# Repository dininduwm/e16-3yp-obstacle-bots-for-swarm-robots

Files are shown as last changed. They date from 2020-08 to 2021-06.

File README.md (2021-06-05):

# Swarm Robotics Platform





### Team
* Members
   * Thushara K A R         :: E/16/369 :: [e16369@eng.pdn.ac.lk](e16369@eng.pdn.ac.lk)
   * Thilakarathna D M D U  :: E/16/366 :: [e16366@eng.pdn.ac.lk](e16366@eng.pdn.ac.lk)
   * Dissanayake D M T H    :: E/16/088 :: [e16088@eng.pdn.ac.lk](e16088@eng.pdn.ac.lk)
* Supervisor
   * Dr. Isuru Navinna
   * Mr. Ziyan Marikkar
   * Prof. Roshan Ragel
   * Dr. Upul Jayasinghe
* Related links
   * [Project Page](https://cepdnaclk.github.io/e16-3yp-obstacle-bots-for-swarm-robots/)
   * [Web Application Home Page](http://3.93.215.173/)
   * [Swarm Dash Board](http://3.93.215.173/swarm/)
   * [Faculty website](http://eng.pdn.ac.lk/)
   * [Department website](http://www.ce.pdn.ac.lk/)
   * [Design Manual](https://github.com/cepdnaclk/e16-3yp-obstacle-bots-for-swarm-robots/blob/master/Documentation/DesignManual.pdf)
   * [User Manual](https://github.com/cepdnaclk/e16-3yp-obstacle-bots-for-swarm-robots/blob/master/Documentation/UserManual.pdf)

### OVERVIEW

In swarm robotics the major barrier is that the researchers have to do a lot of hardware implementation prior to their projects. In this particular project we are going to come up with obstacle bots for a swarm robotic arena which is a part of a swarm robots platform project which eventually solves the above mentioned problem. 

### GOALS

* Automated obstacle bots monitored by an overhead camera setup.

* Bots can move to the desired positions with a user friendly interface.

### SPECIFICATIONS

* Obstacle robot swarm is capable of moving every individual obstacle robot to their own destination with the consideration of  collision  avoidance. 

* With the help of collision avoidance algorithms, obstacle robots can be placed in certain positions which allows the researcher to make  various obstacle shapes on the arena made out of obstacle robot combinations .

* Obstacles can be programmed to be static or dynamic. Dynamic obstacles can model scenarios that have a motion in the obstacle.

* Each robot has its own radio module  which uses a 433Mhz radio band. These modules can be used to communicate with the base station. 

* Each robot has two independent wheels that can perform forward, backward and turning operations. With the help of inbuilt gyroscope robots can perform accurate turning operations.

### SOLUTION ARCHITECTURE
    
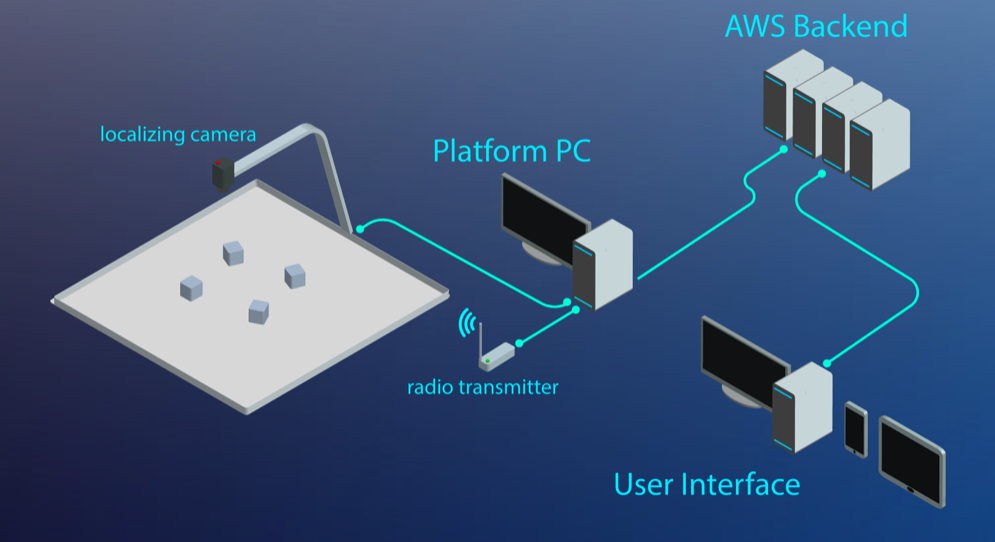
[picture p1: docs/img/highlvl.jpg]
robot_base_design
   
   
### HARDWARE
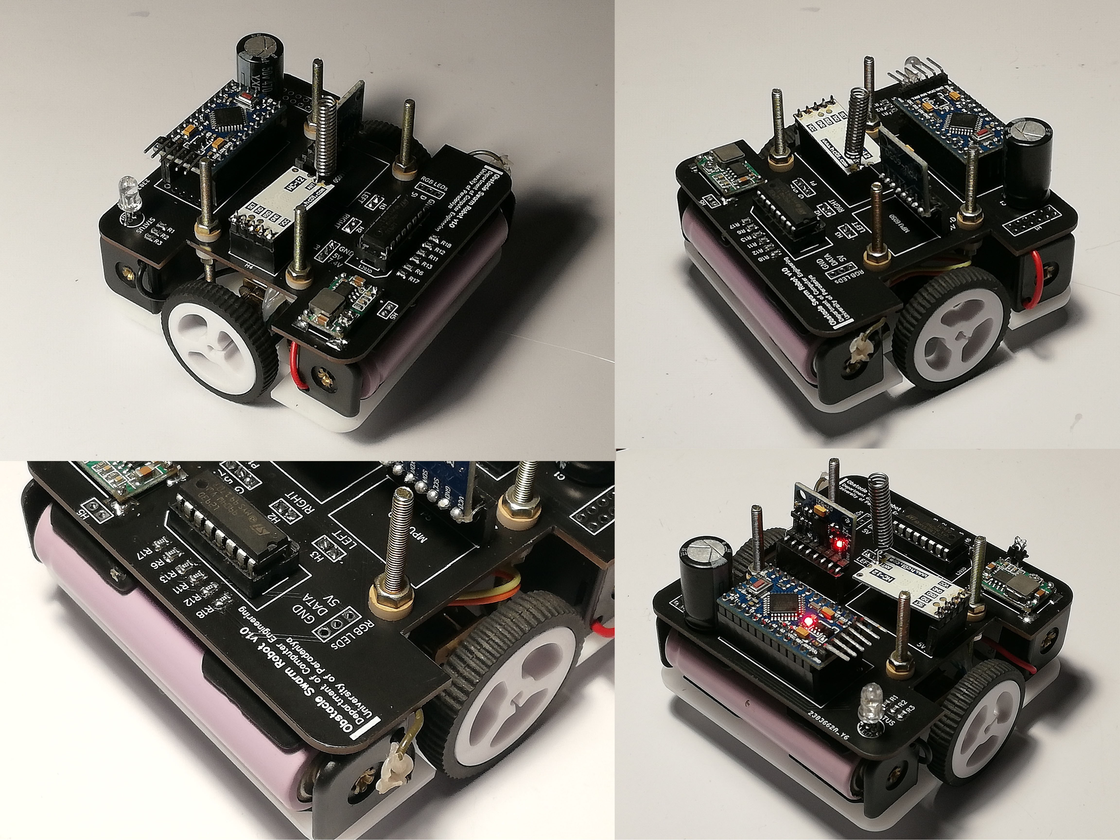
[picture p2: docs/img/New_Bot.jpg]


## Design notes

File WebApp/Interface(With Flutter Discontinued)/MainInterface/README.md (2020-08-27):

# MainInterface

A new Flutter project.

## Getting Started

This project is a starting point for a Flutter application.

A few resources to get you started if this is your first Flutter project:

- [Lab: Write your first Flutter app](https://flutter.dev/docs/get-started/codelab)
- [Cookbook: Useful Flutter samples](https://flutter.dev/docs/cookbook)

For help getting started with Flutter, view our
[online documentation](https://flutter.dev/docs), which offers tutorials,
samples, guidance on mobile development, and a full API reference.

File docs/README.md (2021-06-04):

# Swarm Robotics Platform

### Team
* Members
   * Thushara K A R         :: E/16/369 :: [e16369@eng.pdn.ac.lk](e16369@eng.pdn.ac.lk)
   * Thilakarathna D M D U  :: E/16/366 :: [e16366@eng.pdn.ac.lk](e16366@eng.pdn.ac.lk)
   * Dissanayake D M T H    :: E/16/088 :: [e16088@eng.pdn.ac.lk](e16088@eng.pdn.ac.lk)
* Supervisor
   * Dr. Isuru Navinna
   * Mr. Ziyan Marikkar
   * Prof. Roshan Ragel
   * Dr. Upul Jayasinghe
* Related links
   * [Faculty website](http://eng.pdn.ac.lk/)
   * [Department website](http://www.ce.pdn.ac.lk/)
   * [Web Application Home Page](http://3.93.215.173/)
   * [Swarm Dash Board](http://3.93.215.173/swarm/)
   * [Git Hub Repository](https://github.com/cepdnaclk/e16-3yp-obstacle-bots-for-swarm-robots)
   * [Design Manual](https://github.com/cepdnaclk/e16-3yp-obstacle-bots-for-swarm-robots/blob/master/Documentation/DesignManual.pdf)
   * [User Manual](https://github.com/cepdnaclk/e16-3yp-obstacle-bots-for-swarm-robots/blob/master/Documentation/UserManual.pdf)

### TABLE OF CONTENT

1. >[OVERVIEW](https://github.com/cepdnaclk/e16-3yp-obstacle-bots-for-swarm-robots#overview)
2. >[GOALS](https://github.com/cepdnaclk/e16-3yp-obstacle-bots-for-swarm-robots#goals)
3. >[SPECIFICATIONS](https://github.com/cepdnaclk/e16-3yp-obstacle-bots-for-swarm-robots#specifications)
4. >[SOLUTION ARCHITECTURE](https://github.com/cepdnaclk/e16-3yp-obstacle-bots-for-swarm-robots#solution-architecture)
5. >[HARDWARE](https://github.com/cepdnaclk/e16-3yp-obstacle-bots-for-swarm-robots#hardware)
6. >[WEB INTERFACE](https://github.com/cepdnaclk/e16-3yp-obstacle-bots-for-swarm-robots#software)
7. >[ALGORITHM](https://github.com/cepdnaclk/e16-3yp-obstacle-bots-for-swarm-robots#algorithm)
8. >[TESTING](https://github.com/cepdnaclk/e16-3yp-obstacle-bots-for-swarm-robots#testing)
9. >[BUDGET](https://github.com/cepdnaclk/e16-3yp-obstacle-bots-for-swarm-robots#budget)

### OVERVIEW

In swarm robotics the major barrier is that the researchers have to do a lot of hardware implementation prior to their projects. In this particular project we are going to come up with obstacle bots for a swarm robotic arena which is a part of a swarm robots platform project which eventually solves the above mentioned problem. 

### GOALS

* Automated obstacle bots monitored by an overhead camera setup.

* Bots can move to the desired positions with a user friendly interface.

### SPECIFICATIONS

* Obstacle robot swarm is capable of moving every individual obstacle robot to their own destination with the consideration of  collision  avoidance. 

* With the help of collision avoidance algorithms, obstacle robots can be placed in certain positions which allows the researcher to make  various obstacle shapes on the arena made out of obstacle robot combinations .

* Obstacles can be programmed to be static or dynamic. Dynamic obstacles can model scenarios that have a motion in the obstacle.

* Each robot has its own radio module  which uses a 433Mhz radio band. These modules can be used to communicate with the base station. 

* Each robot has two independent wheels that can perform forward, backward and turning operations. With the help of inbuilt gyroscope robots can perform accurate turning operations.

### SOLUTION ARCHITECTURE
    
   robot_base_design

### HARDWARE

 * #### REAL HARDWARE
    robot_base_design

   STATUS _LED
 * #### 3D MODEL
 
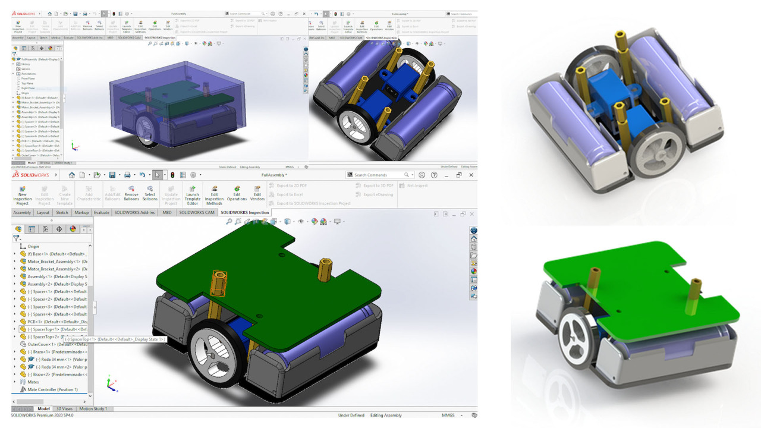
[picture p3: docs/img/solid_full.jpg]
MODEL
   
   
   [3D MODEL DEMO VIDEO](https://drive.google.com/file/d/1BgqnTfJoUTvxhPZTlfKIsdu9cmKUDJUL/view?usp=sharing)

 * #### SAFTY MEASURES

    IMERGENCY STATUS

* #### PCB DESIGN

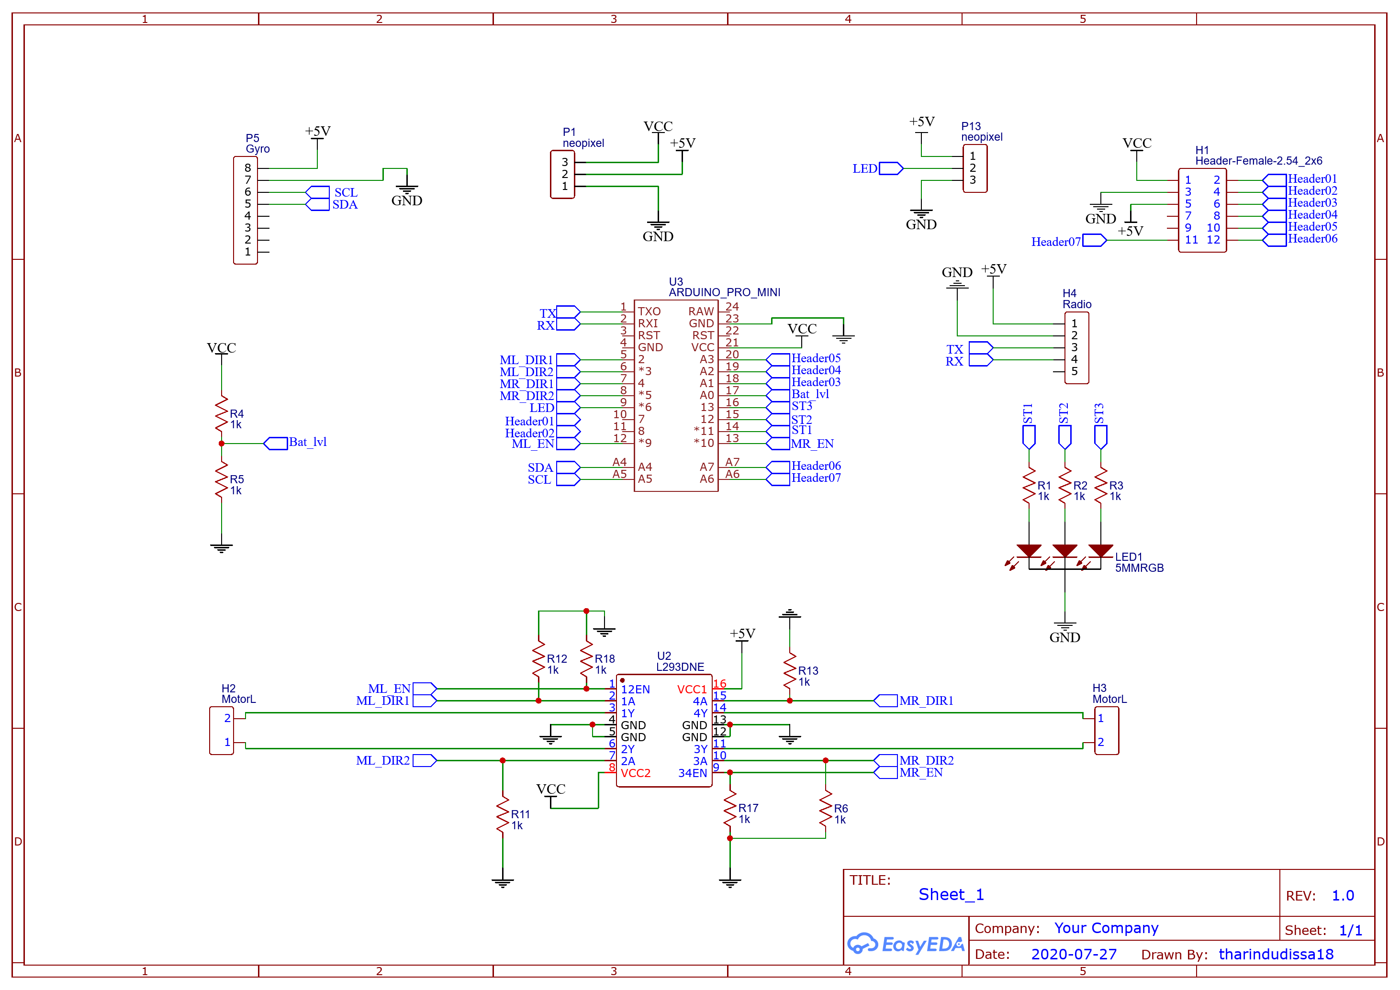
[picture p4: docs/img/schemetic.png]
PCB
  

  PCB
  
  [PCB DEMO VIDEO](https://drive.google.com/file/d/1F948O53cgekAJtsLhbUBktsmgBemvtih/view?usp=sharing)
  
### WEB INTERFACE

   #### Web Interface

   [WEB INTERFACE DEMO VIDEO](https://drive.google.com/file/d/1p-WY_BGf4mX0sW0hUGA0x1Oh4LhzKp-s/view?usp=sharing)

   #### 3D Interface

   [3D INTERFACE DEMO VIDEO](https://drive.google.com/file/d/1X0jq2r_McNR5bppIPc1HjJY1mYPvrYJg/view?usp=sharing)
  
   #### Platform PC Operator GUI

   [3D INTERFACE DEMO VIDEO](https://drive.google.com/file/d/1NqZ_JTVdCaxA32IgvhgPbMnpfuTEIJsR/view?usp=sharing)
  
### ALGORITHM

  ALGORITHM
  
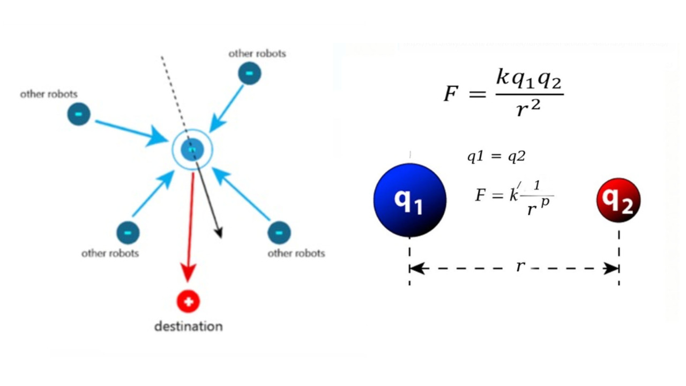
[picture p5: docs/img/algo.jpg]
THEORY
  
  
### TESTING
  
   #### Algorithm Deployment

   [Algorithm Deployment Video](https://drive.google.com/file/d/18J7mnoRWbKy1-WM-fGOGq0C8-KU52HCJ/view?usp=sharing)
  
   #### Web Interface Authentication And Authorization Testing

   [Web Interface Testing Video](https://drive.google.com/file/d/12DfR7rRFpMq2U1c6BGW0rHfQw0c6rsvO/view?usp=sharing)
  
   #### Hardware Testing

   [Hardware Testing Video](https://drive.google.com/file/d/1UNAkzgOKk-umYvnypkwuJJWv3zXbf69Z/view?usp=sharing)
  
### BUDGET
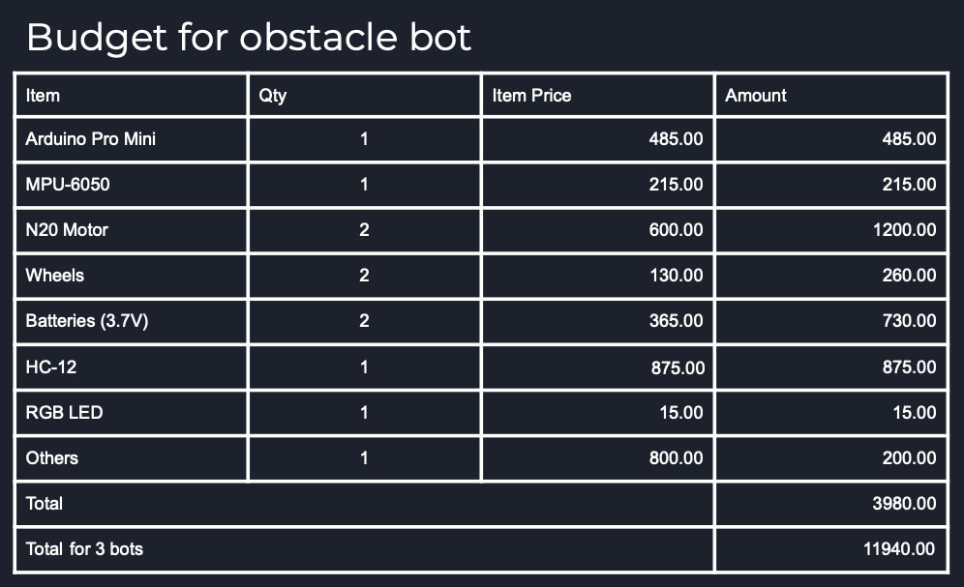
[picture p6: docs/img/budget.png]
BUDGET
  

### FINAL DEMO VIDEO
  [Final Demo Video](https://drive.google.com/file/d/1B5mBls3YdkssftkCu0zrgztlk1W86l-X/view?usp=sharing)
  
### FUTURE IMPROVEMENT
  We plan to run all the algorithms first and then send the data to the robots.
  
  We have to further tune the parameters  to get a smooth process.

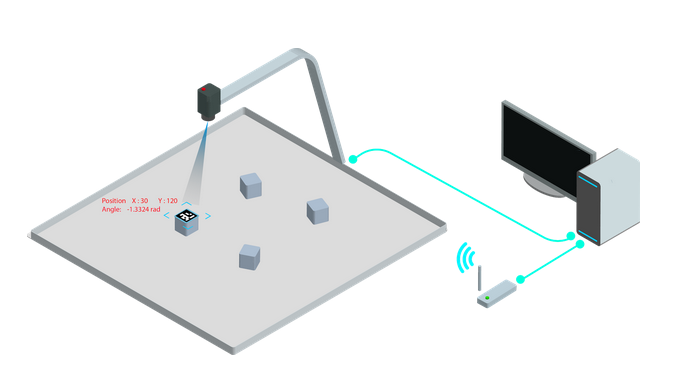
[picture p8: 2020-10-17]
3DModel/Components/Design_Diagrams/robot_arena.png

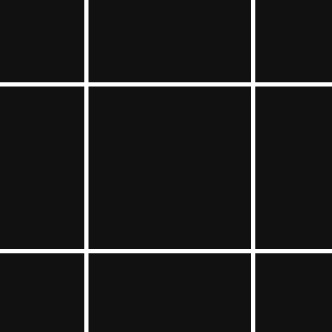
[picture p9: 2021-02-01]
3D_Interface/resources/images/light.jpg

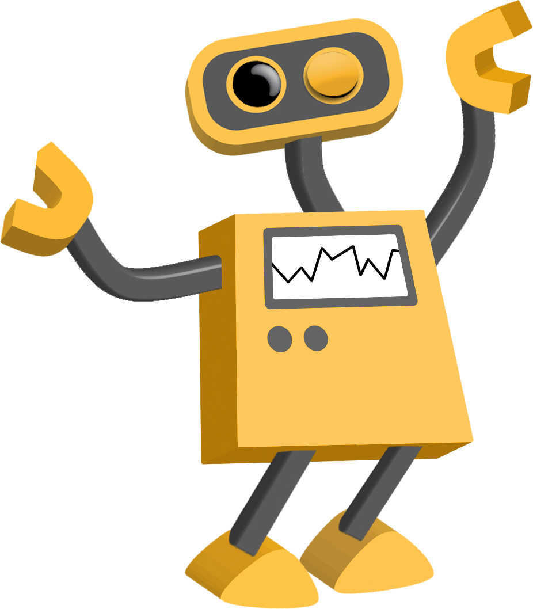
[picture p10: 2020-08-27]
WebApp/Interface(With Flutter Discontinued)/MainInterface/assets/welcomebot.png

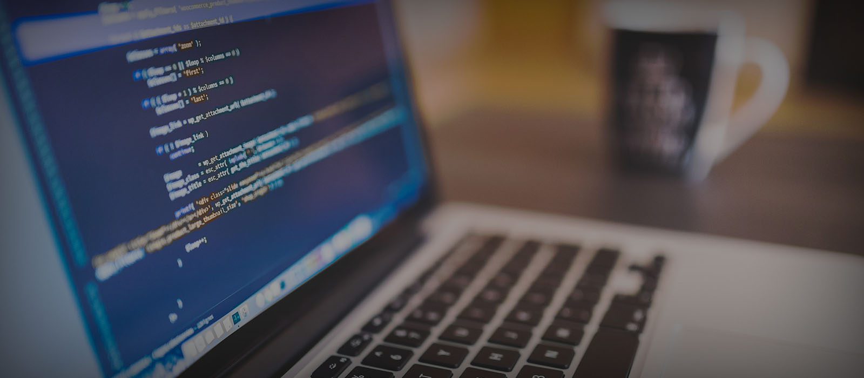
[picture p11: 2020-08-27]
WebApp/Interface(With Flutter Discontinued)/MainInterface/assets/background.jpg

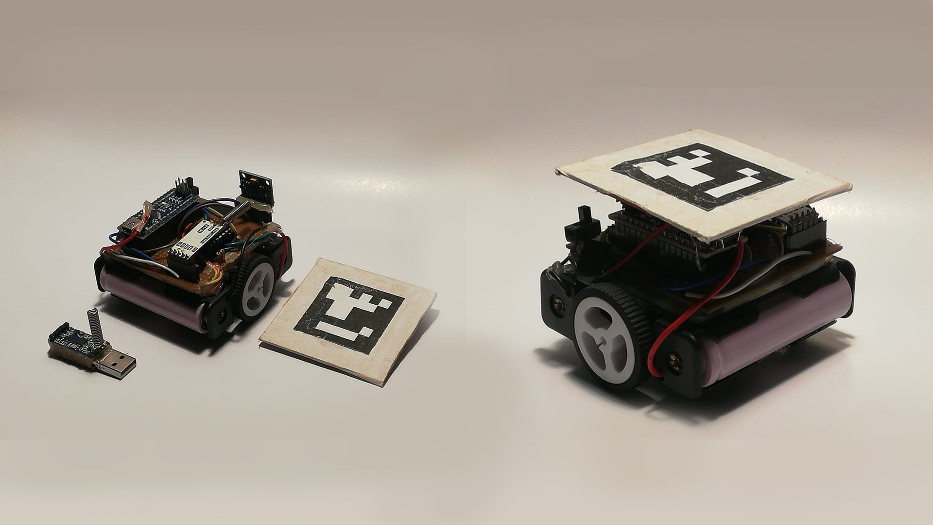
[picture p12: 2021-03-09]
docs/img/proto.jpg

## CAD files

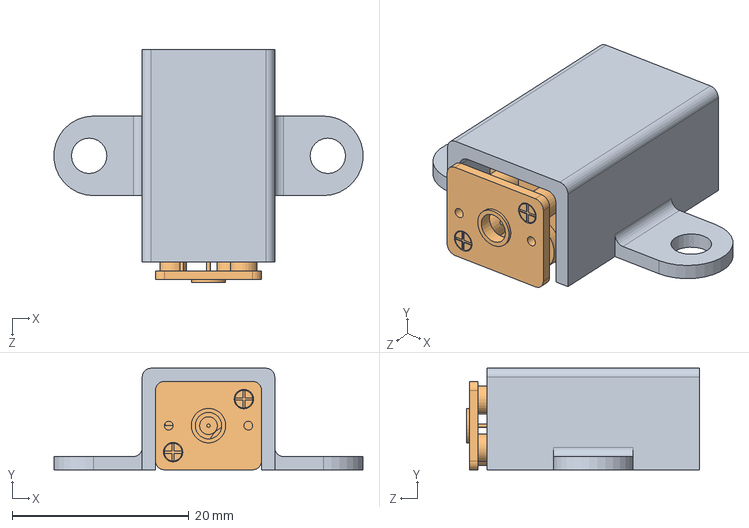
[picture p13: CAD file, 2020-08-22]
3DModel/Components/Motor_Bracket_Assembly/Motor_Bracket_Assembly.SLDASM
35.0 x 11.5 x 26.3 mm
braket pololu
Motor

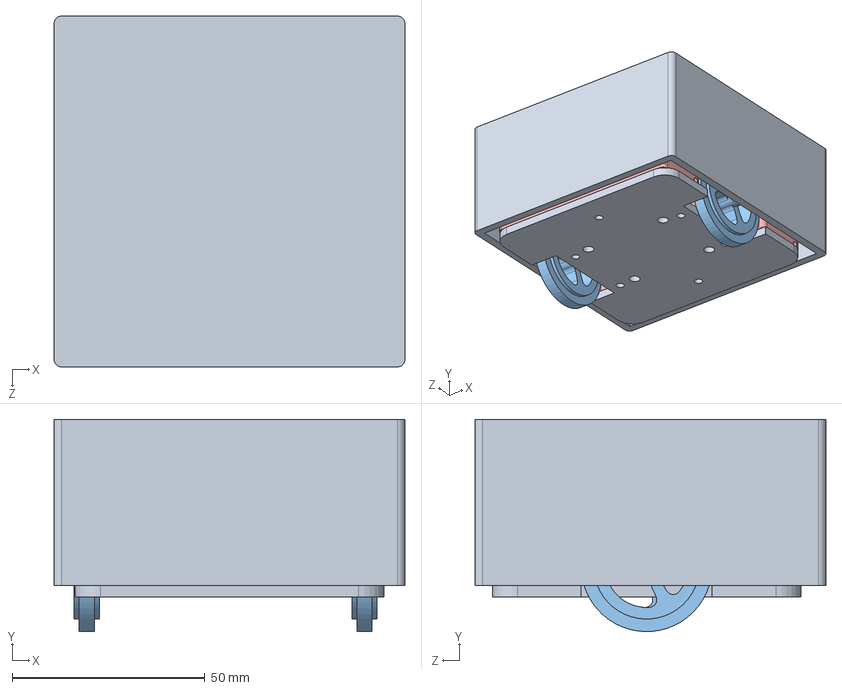
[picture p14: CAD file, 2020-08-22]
3DModel/FullAssembly.SLDASM
91.0 x 55.0 x 91.0 mm
Base
braket pololu x 2
Motor x 2
18650BatteryCase v6.step x 2
Spacer x 4
PCB
SpacerTop x 2
OuterCover
Brazo x 2
Roda 34 mm x 2

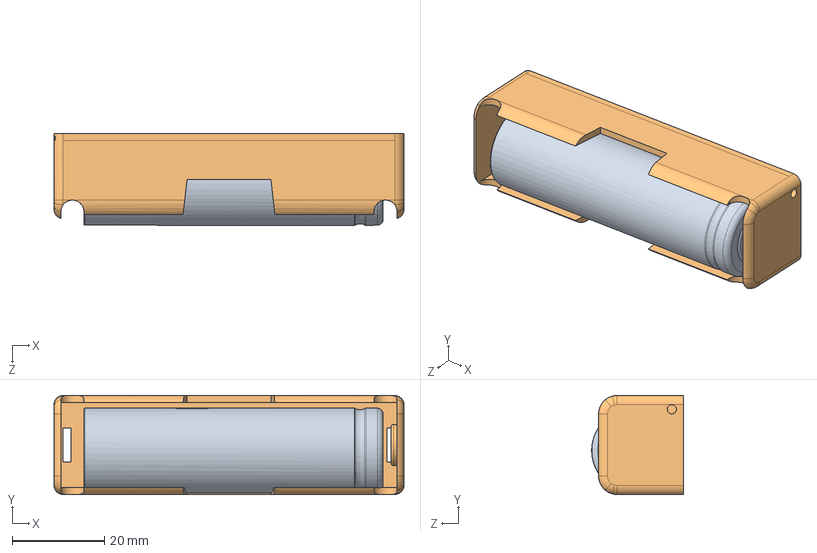
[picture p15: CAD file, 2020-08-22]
3DModel/Components/18650WithCasin/Assembly.SLDASM
76.0 x 21.5 x 19.9 mm
18650BatteryCase v6.step

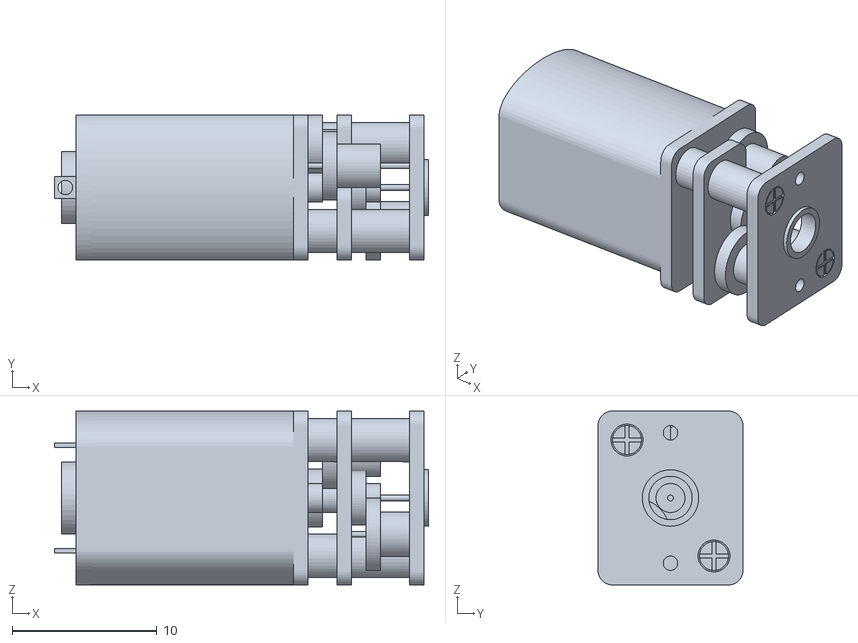
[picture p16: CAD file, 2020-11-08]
3D_Interface/resources/3DModels/motor.STL
25.8 x 10.00 x 12.0

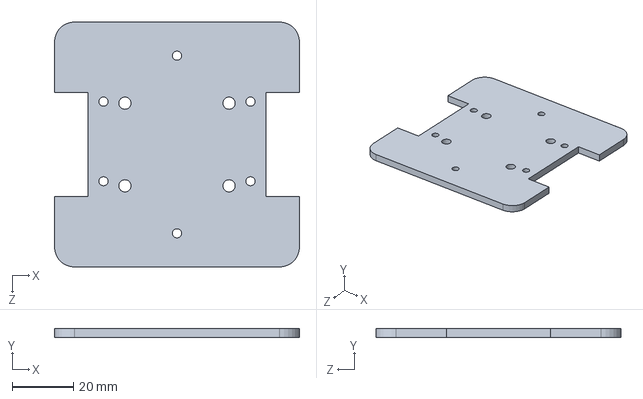
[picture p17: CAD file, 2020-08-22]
3DModel/Components/Base/Base.SLDPRT
80.0 x 3.00 x 80.0 mm

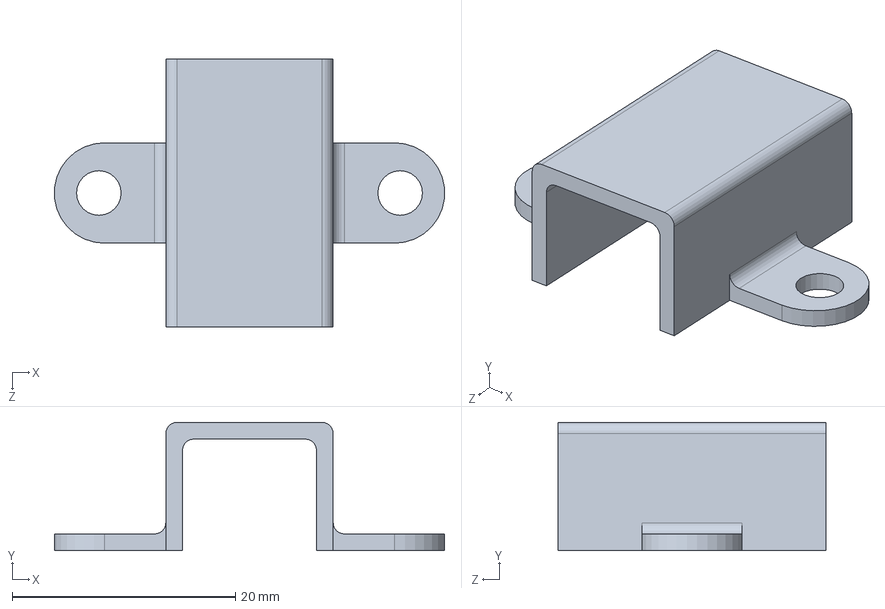
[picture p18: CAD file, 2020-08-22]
3DModel/Components/N20_Bracket/braket pololu.SLDPRT
35.0 x 11.5 x 24.0 mm

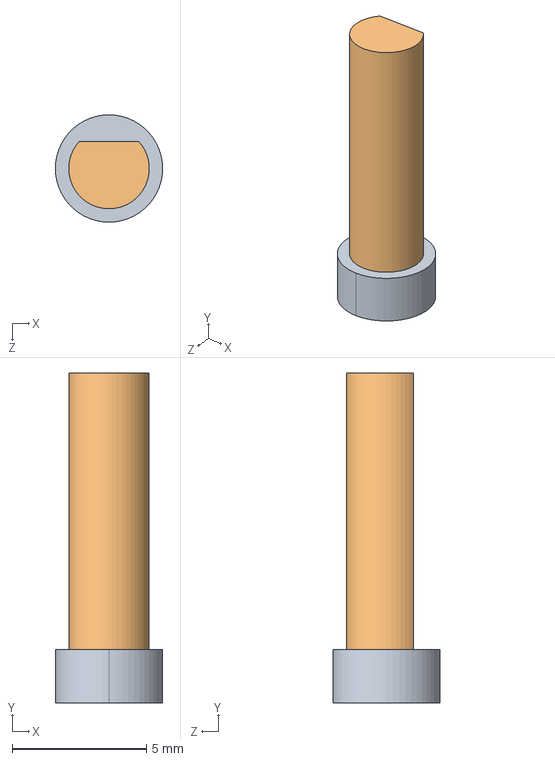
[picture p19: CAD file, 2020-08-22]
3DModel/Components/N20_Motor/Brazo M.STEP
4.00 x 12.3 x 4.00 mm

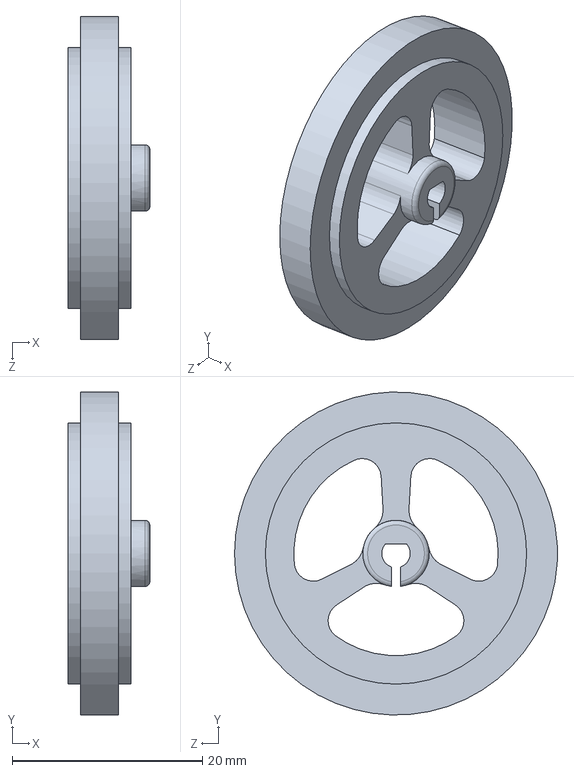
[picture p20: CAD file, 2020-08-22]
3DModel/Components/N20_Wheel/Roda 34 mm.SLDPRT
8.60 x 34.0 x 34.0 mm

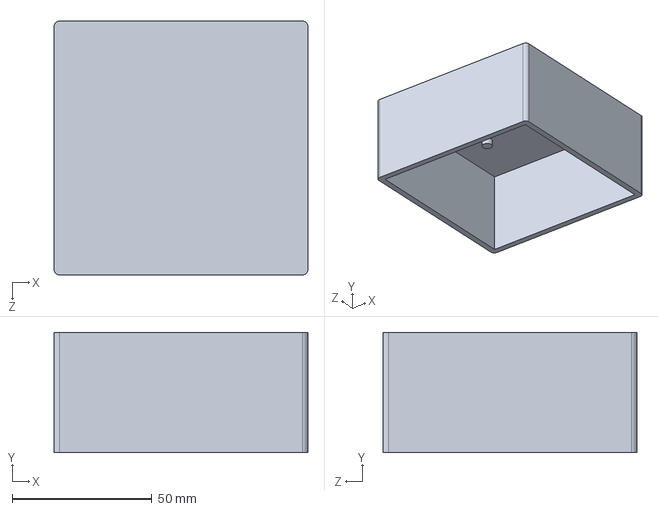
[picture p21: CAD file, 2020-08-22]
3DModel/Components/OuterCover/OuterCover.SLDPRT
91.0 x 43.0 x 91.0 mm

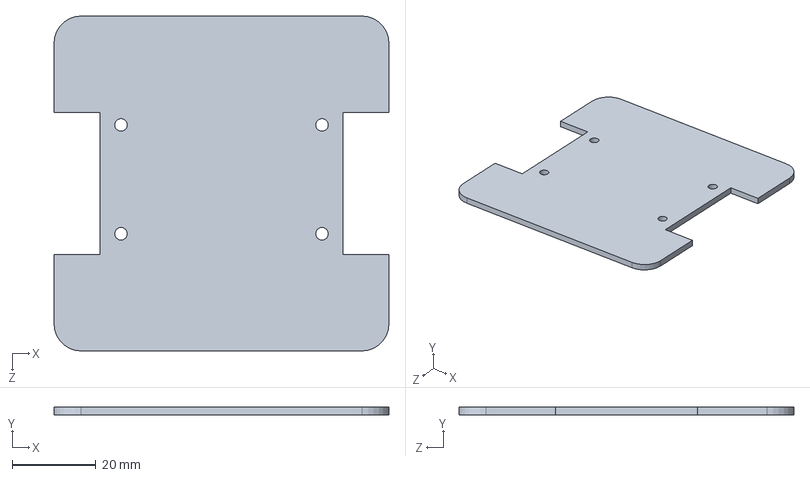
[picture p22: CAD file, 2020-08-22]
3DModel/Components/PCB/PCB.SLDPRT
80.0 x 2.00 x 80.0 mm

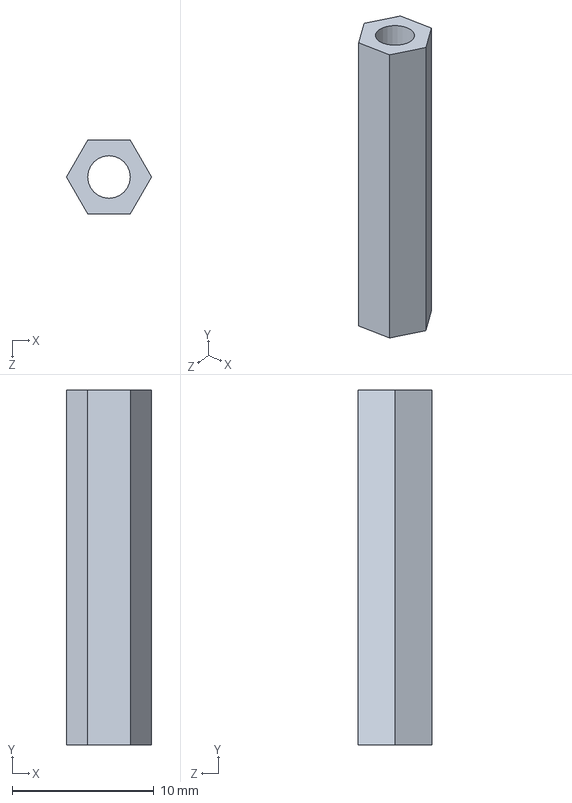
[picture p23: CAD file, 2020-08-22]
3DModel/Components/Spacer/Spacer.SLDPRT
6.00 x 25.0 x 5.20 mm

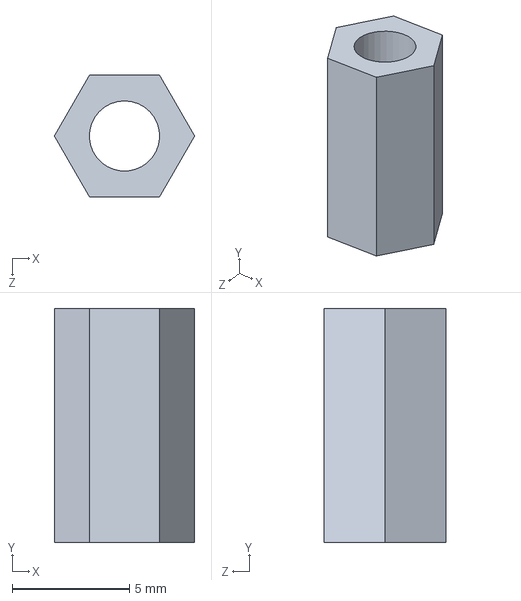
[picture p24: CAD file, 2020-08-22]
3DModel/Components/SpacerTop/SpacerTop.SLDPRT
6.00 x 10.0 x 5.20 mm

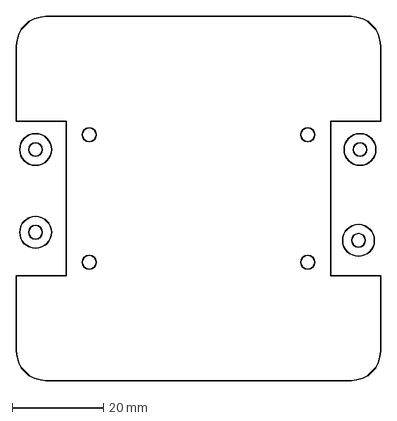
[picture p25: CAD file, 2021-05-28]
Fabrication/Laser Cutting/BasePlate/bot.dxf
80.0 x 80.0 mm

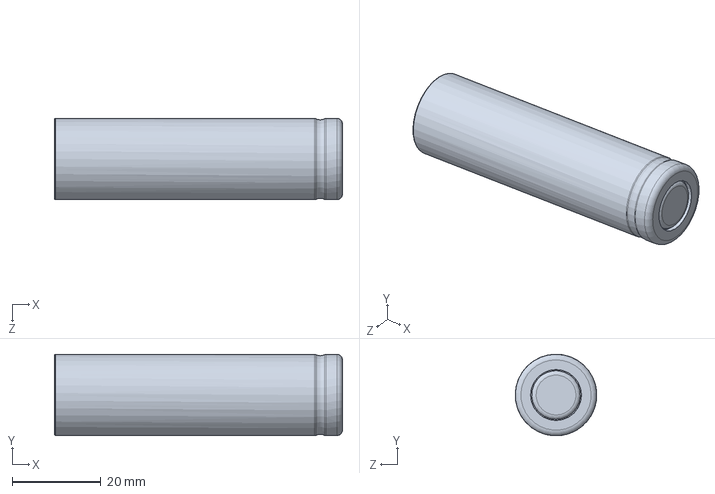
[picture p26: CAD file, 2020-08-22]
3DModel/Components/18650WithCasin/18650.SLDPRT
65.0 x 18.4 x 18.4 mm

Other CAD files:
WebApp/MainWebApp/static/swarm/Cover.91c86dd7.STL
3DModel/Components/N20_Motor/Brazo.SLDPRT
3DModel/Components/N20_Motor/Motor M.STEP
3DModel/Components/N20_Motor/Motor.SLDPRT
3DModel/Components/18650WithCasin/18650BatteryCase v6.step

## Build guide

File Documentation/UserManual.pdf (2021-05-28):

# User Manual

# Obstacle Robots For Swarm Robots Platform

May 2021

ISSUED BY
Department of Computer Engineering, University of Peradeniya.

REPRESENTATIVE
E/16/369 Rusiru Thushara
E/16/366 Dinindu Thilakarathne E/16/088 Heshan Disanayake

# Content

1. Introduction & Background | 3
2. Features | 4
3. Quick Startup | 5
4. Device Installation | 7
5. Operator GUI | 8
6. Web Interface | 9
6.2. | Indicators | |
| 10

### 6.3.3. Removing a destination | 12

6.3.4. | Remove all destinations | | 12

### 6.3.5. Changing the robot’s colour | 12

7. Robot | | 13

### 7.1. Overview | 13

8. Troubleshooting | 15

### 8.1. Camera position troubleshooting | 15 8.2. AR marker detection troubleshooting | 15 8.3. Local communication troubleshooting | 15 8.4. Robottroubleshooting | 16

# List of Figures

Figure 1: High-Level Diagram | 3
Figure 2: Operator GUI | 8
Figure 3: Web interface | 10
Figure 4: Overview ofthe robot | 13

# 1. Introduction and Background

### 1.1. Process Overview

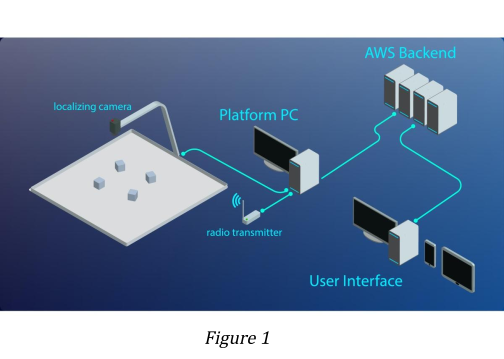
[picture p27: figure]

The system uses an overhead camera to localize the robots and the video feed is sent to the platform PC where all the algorithms are running and calculating the required parameters and the relevant data to the robots are sent using radio transmission and the other required data is sent to the server backend.

### 1.2. The System

The system contains a radio transmitter module, camera module, and robots. You should have to have an arena for the given dimensions. If your arena dimensions are higher than the given dimensions you have to purchase a separate HD overhead camera module. You have to have a computer ( not included with the product ) with an internet connection.

# 2. Features

- Algorithms are capable of handling about 100 robots.
- Self homing feature when the battery levels are too low.
- Battery level monitoring feature with GUI.
- Hardware and software emergency stop buttons.
- User-friendly 3D web interface.
- User-friendly operator GUI.
- Compact robot designing.
- Highly accurate positioning of robots.
- Colour changing capability of robots.
- Automatic error detections of robots.

# 3. Quick Startup

This section explains the quicker way to set up the system to use

### 1. Setting up the overhead camera

Overhead camera should be fixed about 2m from the top surface of the arena. Then the USB cable should connect to the platform PC. (Camera calibration have to be done after step 2)

### 2. Installing and setting up the operator GUI

a. First, you have to install and set up python3 and pip3 in your system.
b. Then you have to clone this repository. https://github.com/cepdnaclk/e16-3yp-obstacle-bots-for-swarm-robots.git
c. Then change the directory to,/Platform_PC_Software/MainCode/

cd /Platform_PC_Software/MainCode/
d. Next open a terminal in that directory and enter the following command

pip3 install -r req.txt

### 3. Installing and setting up the radio transmitter module

a. You have to plugin the provided radio transmitter module to a USB port on the Computer
b. You have to identify the COM port for the usb device

### 4. Starting the Operator GUI for the firsttime

a. You will be prompted to enter the Swarm Name, Swarm ID, and the COM Portfor the radio transmitter module.
b. Now you can see the Operator GUI for the First time.

### 5. Adjusting the camera position

a. You have to adjust the camera position in such a way that the whole camera feed fits to the camera view.

b. Next place a bot inside the arena (Don’t turn on the robot yet). Observe the camera feed and verify the AR marker has been identified. (If identified, you can see a green square around the marker )

### 6. Turning on the robot

a. Now you can turn on the robot.
b. Then click the start button on the Operator GUI.
c. Then the robot should turn to a 90-degree angle and the status light should turn into cyan colour.
d. Now click on the home button in the control panel.
e. Then the robot should be moved into the home position.
(Note:- If you have any issues please refer to the troubleshooting section)

# 4. Device Installation

### 4.1. Power Requirements

- You have to install two 18650 Li-ion batteries on a robot. You have to charge each and every battery for at least 3 hours.
- A 24v power supply should be connected to the status lamp.

### 4.2. Network Configuration

- Platform PCs should always be connected to the internet. ( No other specific configuration needed )

### 4.3. Configuring Camera Setup

- The camera should be fixed, about 2m from the top surface of the arena.
- Then adjust the camera view by looking at the camera image in the Operator GUI (the whole arena should be visible through the camera view )
- Then you have to place a robot inside the camera view ( Without turning on the robot )
- Make sure the robot is identified by the Operator GUI by drawing a green square around the AR marker.
(Note:- If the markers are not detecting. Please refer to the camera troubleshooting section)

### 4.4. Radio Transmitter Installation

- The radio transmitter should be plugged into a USB port
- You should find the COM port for the transmitter
- You will be prompted to ask the COM port of the radio transmitter when opening the Operator GUI.

### 4.5. Emergency Stop and Status Lamp Installation

- The status lamp should be fixed on the arena
- Emergency stop should be fixed near to the operator
- Both of them should be connected to the radio transmitter module.
- Given 24V power supply should be connected to the status lamp.

# 5. Operator GUI

### 5.1. Overview

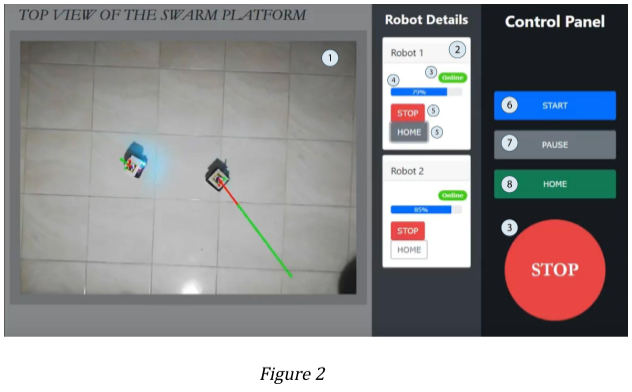
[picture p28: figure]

1 - Live view
2 - Robot details
3 - Robotlive status
4 - Battery percentage

5 - Individual Stop
6 - Individual Home
7 - Start button
8 - Pause button

9 - All Home Button
10 - All Stop Button

### 5.2. Indicators

The operator can check the battery status of the robots using the [4] battery status progress bar. Also, use the [3] status indicator to check the online/offline status of the robots.

### 5.3. Controlling

- Adding a new robot

The system will auto-detect a robot once you are adding a new robot to the system.
- Homing a robot
Press button 5 of individual robots to move the individual robot to the home position.
- Software emergency stop
Press the emergency stop button (button no. 3) to stop all the robots in an emergency.
- Starting and pausing a sequence
Press button 6 and 7 to start and pause the robots.

# 6. Web Interface

### 6.1. Overview

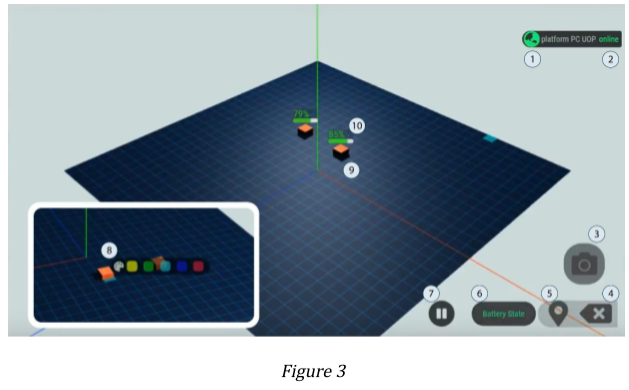
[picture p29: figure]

1 - Server name
2 - Server status
3 - Camera controller
4 - Destination clear

5 - Destination setter
6 - Battery status
7 - Pause button
8 - Robot colour picker

9 - Robot
10 - Battery level

### 6.2. Indicators

- Server Status

The status of the server can be seen in this tag. The globe will be animated if the server is online. Also, you can see the platform name in this tag.

- Robot Battery status

The battery status of the robot can be activated through the battery status button.

### 6.3. Controlling 6.3.1. Change the camera view

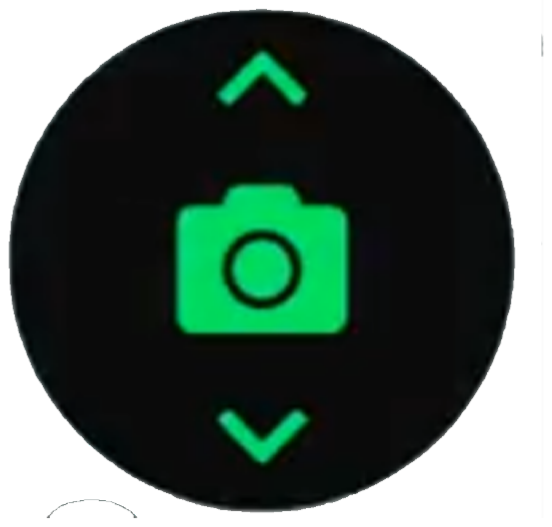
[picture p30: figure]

This is the controller for the camera view. The upper arrow has the control to align the camera view to the top view. And the middle camera logo is the button for isometric camera angle(camera home).

### 6.3.2. Setting a destination

To set the destinations you have to first toggle into destination set mode by clicking this button. Then you can set the destinations up to the count of robots by clicking on the arena. After deciding the destination positions you can release this button to transmit the destination data to the platform PC.

### 6.3.3. Removing a destination

To remove a single destination, click the destination button to go to the destination set mode. Then click on the destination you need to remove. Then the indication of the destination will go away.

6.3.4. Remove all destinations.

Click on this button to remove all destinations.

### 6.3.5. Change the color

To change the color, hover over the color pallet to get the color selecting option.choose a color you want .

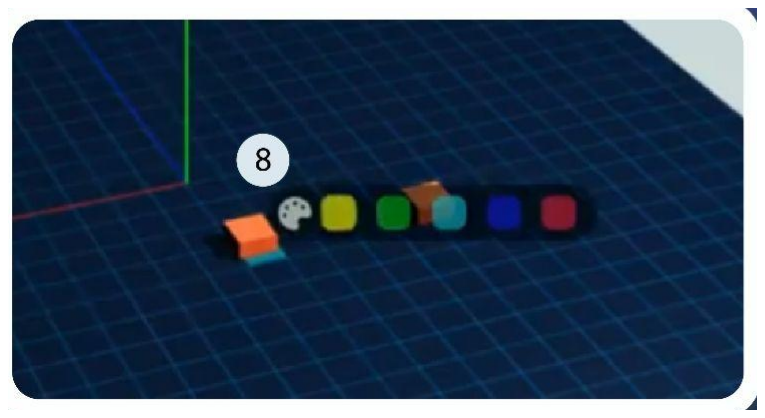
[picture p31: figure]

# 7. Robot

7.1. Overview

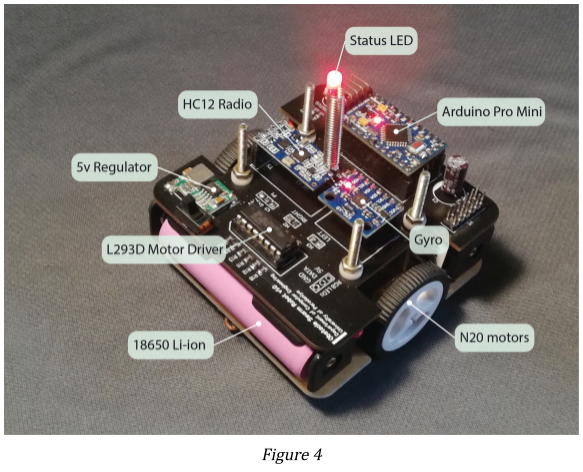
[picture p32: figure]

- Arduino pro mini
- Arduino 328p 16mhz microcontroller is used as the computer of this robot
- HC12 Radio module
- The radio communication is done with a 433Mhz HC-12 module. This is the transceiver that has the capability of 2-way communication with the platform PC.
- Gyroscope
- MPU 6050 is the gyroscope module used in this robot.

- 5v Regulator.
- Switch Mode 5v voltage regulator.
- Motor driver
- L293D is the motor driver IC used in this robot. Since this is the D version internal circuitry is safe from the flyback voltages.
- Batteries
- This robot is powered with 2s 18650 2000mah Li-ion battery.
- Motors
- This robot has two N20 100rpm 6v motors with 30mmx7mm wheels.
- Status LED
- Red blinking - robot successfully received a data packet.
- Blue blinking - robot successfully received a data packet that belong to the specific robot.
- Green - robot is in the turning PID loop.
- Light Blue - Robot at the destination.
- Extension port
- For the further development the unused pins of the arduino are extended via male 6x2 header the pin description is as follows.

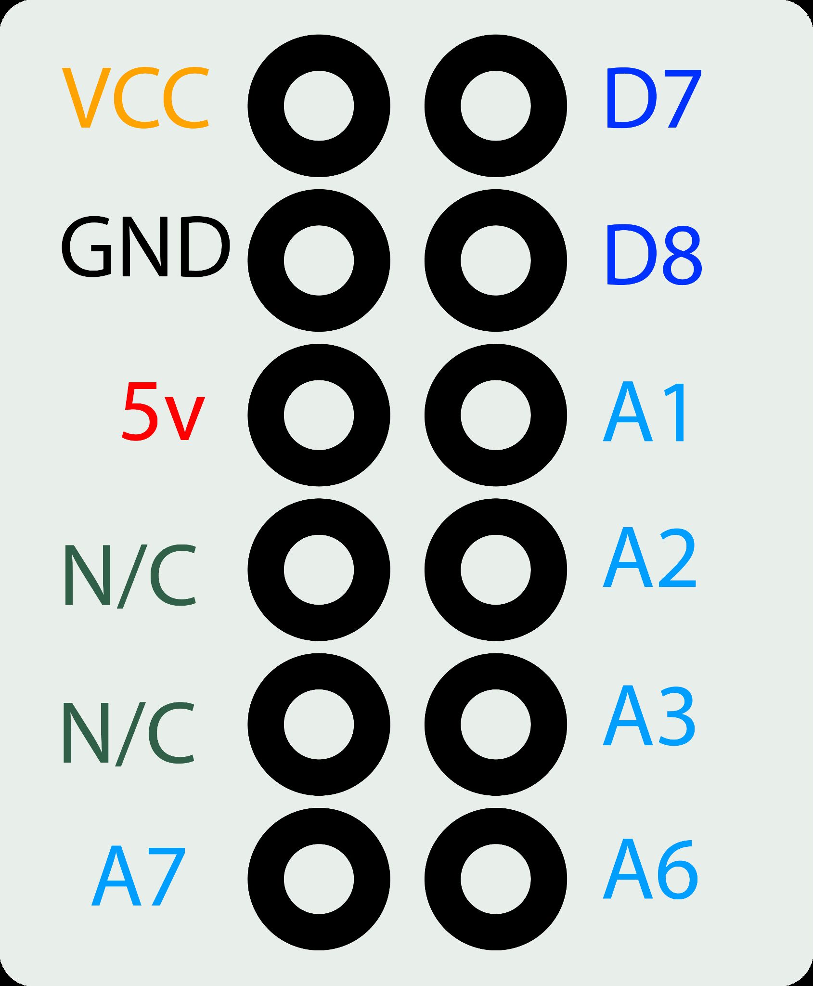
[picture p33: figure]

# 8. Troubleshooting

### 8.1. Camera position troubleshooting

Problem | Solution
Camera view detecting only part of the arena | ● Move the camera upwards until you can see the whole arena ● Center the camera module in the Arena
Camera not detecting | ● Unplug the USB cable and plug it again
Camera feed interruption ( or lagging ) | ● Check for the CPU usage of the system. If the CPU usage is above 80%, kill unwanted processes.

### 8.2. AR marker detection troubleshooting

Problem | Solution
AR Markers not detecting | ● Adjust the lighting conditions ● Move the camera closer to the Arena

### 8.3. Local communication troubleshooting

Problem | Solution
If the blue LED on the transmitter not blinking rapidly | ● Unplug the radio transmitter and plug it again ● Check whether the COM port is correct
Robotsred light not blinking | ● Check whether the Robot ids are correct in the Operator GUI ● Reset the Robot

- Reduce the distance between the radio transmitter and the Arena
- Check the radio transmitter module is firmly attached to the PCB

### 8.4. Robottroubleshooting

Problem | Solution
Not turning ON | ● Check whether the batteries are charged ● Check the batteries are installed in the correct way
One or both wheels not turning | ● Check the pugs connected to the motors are firmly attached to the PCB ● Check the wheels are firmly attached to the motor ● Check the battery level.
Robot is oscillating | ● Run the robot calibration programme

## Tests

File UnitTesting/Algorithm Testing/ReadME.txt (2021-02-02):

######
This will test the collition avoiding and positioning algorithm.

Cange the required bot count in the UnitTest.py file
Then, run the UnitTest.py

> python3 UnitTest.py

######

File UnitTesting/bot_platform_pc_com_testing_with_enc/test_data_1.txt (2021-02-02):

{'1': [118, 115, 85, 22], '2': [135, 320, 400, 291]}
{'1': [416, 49, 226, 333], '2': [207, 338, 443, 345]}
{'1': [260, 187, 94, 340], '2': [206, 324, 171, 8]}
{'1': [285, 288, 188, 8], '2': [313, 171, 381, 201]}
{'1': [301, 162, 341, 261], '2': [103, 193, 198, 201]}
{'1': [181, 167, 330, 13], '2': [66, 84, 172, 185]}
{'1': [30, 199, 179, 2], '2': [68, 274, 62, 169]}
{'1': [133, 124, 178, 68], '2': [272, 192, 247, 96]}
{'1': [323, 163, 446, 321], '2': [125, 68, 192, 157]}
{'1': [188, 290, 338, 40], '2': [61, 326, 78, 336]}

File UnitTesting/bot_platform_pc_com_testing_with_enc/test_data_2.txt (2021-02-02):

b'serial test 0021\r\n'
b'1,118,115,85,22,\n'
b'2,135,320,400,291,\n'
b'1,416,49,226,333,\n'
b'2,207,338,443,345,\n'
b'1,260,187,94,340,\n'
b'2,206,324,171,8,\n'
b'1,285,288,188,8,\n'
b'2,313,171,381,201,\n'
b'1,301,162,341,261,\n'
b'2,103,193,198,201,\n'
b'1,181,167,330,13,\n'
b'2,66,84,172,185,\n'
b'1,30,199,179,2,\n'
b'2,68,274,62,169,\n'
b'1,133,124,178,68,\n'
b'2,272,192,247,96,\n'
b'1,323,163,446,321,\n'
b'2,125,68,192,1571,188,290,338,42,61,326,78,336\r\n'

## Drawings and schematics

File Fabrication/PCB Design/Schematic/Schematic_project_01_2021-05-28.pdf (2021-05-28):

# VCCBATT

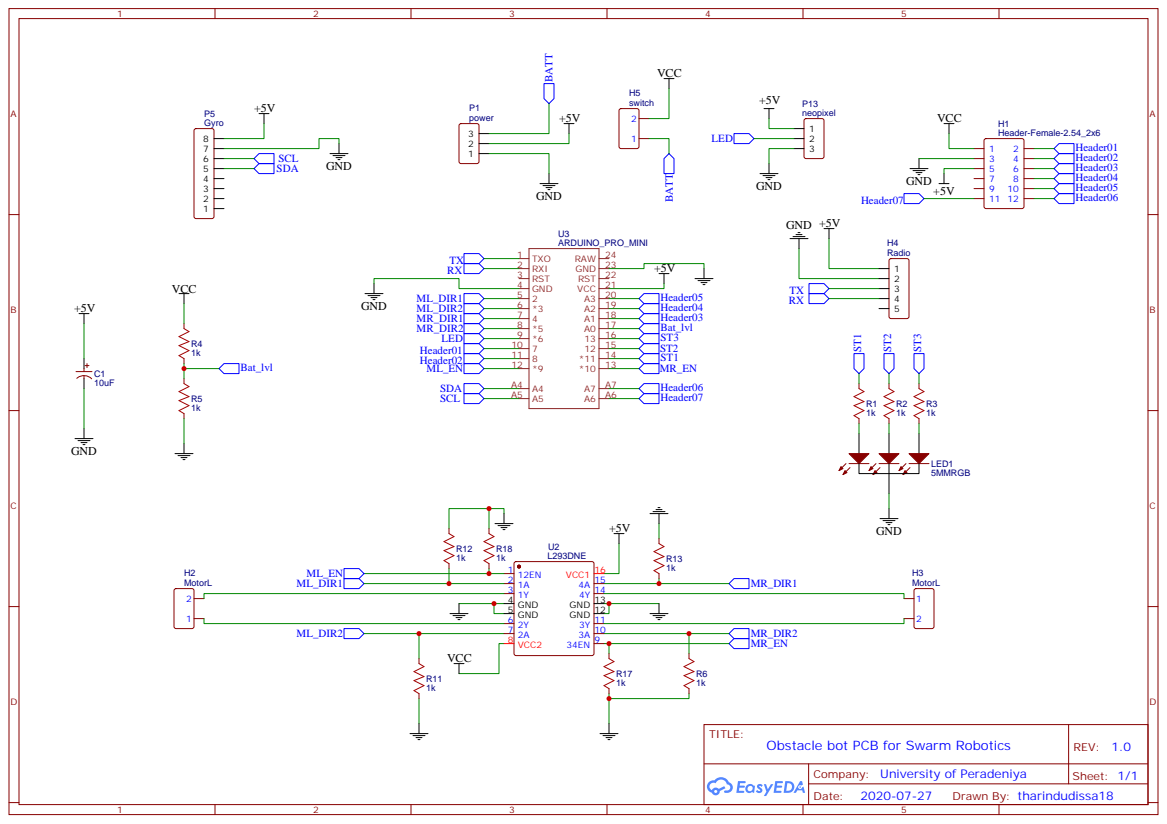
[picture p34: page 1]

Company: University of Peradeniya

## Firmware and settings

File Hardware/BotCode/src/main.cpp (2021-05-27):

#include <PID_v1.h>
#include <Wire.h>

#define EN_R 9  // right motor enable
#define EN_L 10 // left motor enable

#define ML_A1 5 // left motor in 1
#define ML_A2 4 // left motor in 2

#define MR_A1 3 // right motor in 1
#define MR_A2 2 // right motor in 2

#define led_r 11 // status leds
#define led_g 12
#define led_b 13

const float turningThresh = 0.15; // threshold to stop turning
const double distThresh = 20;     // threshold to stop moving
const int MPU = 0x68;             // MPU6050 I2C address
float GyroX, GyroY, GyroZ;
float angle;                                  // Gyro angle
float GyroErrorX;                             // Gyro error
float elapsedTime, currentTime, previousTime; // time stamps for gyro calculaions
int c = 0;

bool idflag = false;
String id = "";
double arr[3]{};   // arr to hold startAngle, travelDis, endAngle
int idx = 0;     // index to track the arr index
bool good = false; // bool to check the correct id

//json decoded
double startAngle, endAngle, travelDis;

//PID variables
double Setpoint, Input, Output;
bool newData = false;

// id of the bot
String myID = "1";

// creating software serial object


// variables to hold temp data
String reciveStr = "";

//PID configuration
PID myPID(&Input, &Output, &Setpoint, 16, 0, 0.23, DIRECT);

void ML(int val)
{ // motor function left(val : speed value)

  //handle overflow in val
  if (val < -255)
  {
    val = -255;
  }
  else if (val > 255)
  {
    val = 255;
  }

  if (val > 0) // if the motor speed is positive
  {
    digitalWrite(ML_A2, HIGH); // set the motor control signals
    digitalWrite(ML_A1, LOW);
    analogWrite(EN_L, val); // give pwm signal to motor enable
  }
  else
  {
    digitalWrite(ML_A2, LOW); // set the motor control signals
    digitalWrite(ML_A1, HIGH);
    analogWrite(EN_L, abs(val)); // give pwm signal to motor enable
  }
}

void MR(int val)
{ // motor function right(val : speed value)

  //handle overflow in val
  if (val < -255)
  {
    val = -255;
  }
  else if (val > 255)
  {
    val = 255;
  }

  if (val > 0) // if the motor speed is positive
  {

    digitalWrite(MR_A1, HIGH); // set the motor control signals
    digitalWrite(MR_A2, LOW);
    analogWrite(EN_R, val); // give pwm signal to motor enable
  }
  else
  {
    digitalWrite(MR_A1, LOW); // set the motor control signals
    digitalWrite(MR_A2, HIGH);
    analogWrite(EN_R, abs(val)); // give pwm signal to motor enable
  }
}


void setup()
{
  pinMode(EN_R, OUTPUT);
  pinMode(EN_L, OUTPUT);
  pinMode(MR_A1, OUTPUT);
  pinMode(MR_A2, OUTPUT);
  pinMode(ML_A1, OUTPUT);
  pinMode(ML_A2, OUTPUT);
  pinMode(led_r, OUTPUT);
  pinMode(led_g, OUTPUT);
  pinMode(led_b, OUTPUT);

  // begining the serial commiunication



  myPID.SetOutputLimits(-255, 255); // limits of the PID output
  myPID.SetSampleTime(20);          // refresh rate of the PID
  myPID.SetMode(AUTOMATIC);
  Setpoint = 0;

  calculate_IMU_error(); // calculate the Gyro module error
  delay(20);
//  Serial.println("Bot initiated");

  intShow();
}

bool turningDone = false; // flag true if tuning is done
bool movingDone = false;  // flag true if robot at the destination
double prvstartAngle = 0; // vaiable used to track start angle changes
double spd = 125;         // speed of the movements: [-255, 255]

int tcount = 0;
double dirCorrection = -1;
double prevDist = 0;

void loop()
{
//  Setpoint = PI/2;  
//  
  while(true){
    for(int i =1; i<8; i++){
      LED(i);
      delay(100);
      LED(0);
      delay(100);
      LED(i);
      delay(100);
      LED(0);
      delay(1000);
      }  
    }
  if (Serial.available() > 0)
  {

    dataDecoder(Serial.read()); // parsing the json string
    LED(0);
  }

  // start turning process if the start angle is above the "turningThresh"
  if ((-turningThresh > startAngle) || (turningThresh < startAngle))
  {

    turn();
    LED(0);
  }

  // set the movingDone flag if the robo is at the destination
  if (travelDis < distThresh)
  {

    movingDone = true;
  }
  else
  {

    movingDone = false;
  }

  if ((tcount < 40) && turningDone && newData && !movingDone) //run motors with PID if conditions are satisfied
  {
    Setpoint = 0; // set the gyro setpoint to 0
    updateGyro();
    Input = (double)angle;
    myPID.Compute();
    ML(spd - Output);
    MR(spd + Output);
  }
  else
  {
    LED(0);
    newData = false;
    ML(0);
    MR(0);
  }

  tcount++;
  delay(5);
}

void turn()
{ 
  
  turningDone = false;
  angle = 0;                               //set the current angle to zer0
  Setpoint = -1 * radToDegree(startAngle); // set the setpoint as the startAngle

  prvstartAngle = startAngle; // update the prvstartAngle
//  Serial.println("started turning PID " + String(startAngle));

  while (!turningDone)
  {
    LED(2); //green
    if (Serial.available() > 0)
    {
      // parsing the json string
      dataDecoder(Serial.read());
    }

    if (prvstartAngle != startAngle) // if there any changes in startAngle, set the current angle to zero and set the set point
    {
      Setpoint = -1 * radToDegree(startAngle);
      angle = 0;
      prvstartAngle = startAngle;
    }
    updateGyro();
    Input = (double)angle;
    myPID.Compute();

    // Serial.println(String(startAngle) + ", " + String(Setpoint) + ", " + String(Input) + ", " + String(Output) + ", ");

    ML(-Output);
    MR(Output);
    if ((-turningThresh < startAngle) && (turningThresh > startAngle)) // exit form the loop if the startAngle is bounded in threshold
    {
//      Serial.println("turning done");
      turningDone = true;
    }
    LED(0); //off
  }
  angle = 0;
  ML(0);
  MR(0);




 
}


void updateGyro()
{
  previousTime = currentTime;                        // Previous time is stored before the actual time read
  currentTime = millis();                            // Current time actual time read
  elapsedTime = (currentTime - previousTime) / 1000; // Divide by 1000 to get seconds
  Wire.beginTransmission(MPU);
  Wire.write(0x43); // Gyro data first register address 0x43
  Wire.endTransmission(false);
  Wire.requestFrom(MPU, 6, true);                   // Read 4 registers total, each axis value is stored in 2 registers
  GyroX = (Wire.read() << 8 | Wire.read()) / 32.75; // For a 1000deg/s range we have to divide first the raw value by 131.0, according to the datasheet
  GyroY = (Wire.read() << 8 | Wire.read()) / 131.0;
  GyroZ = (Wire.read() << 8 | Wire.read()) / 32.75;
  GyroZ = GyroZ - (-0.25); //GyroErrorX; // GyroErrorX ~(-0.56)

  angle = angle + GyroZ * elapsedTime; // deg/s * s = deg
  // Serial.println(GyroX);
}

double radToDegree(double rads)
{
  return (float)(rads * 180 / PI);
}

// function to calculate the gyro error
void calculate_IMU_error()
{
  // init the gyro0
  Wire.begin();                // Initialize comunication
  Wire.beginTransmission(MPU); // Start communication with MPU6050 // MPU=0x68
  Wire.write(0x6B);            // Talk to 0 register 6B
  Wire.write(0x00);            // reset
  Wire.endTransmission(true);

  Wire.beginTransmission(MPU);
  Wire.write(0x1B); // Talk to the GYRO_CONFIG register (1B hex)
  Wire.write(0x10); // Set the register bits as 00010000 (1000deg/s full scale)
  Wire.endTransmission(true);
  delay(20);

  // Read gyro values 200 times
  while (c < 200)
  {
    Wire.beginTransmission(MPU);
    Wire.write(0x43);
    Wire.endTransmission(false);
    Wire.requestFrom(MPU, 6, true);
    GyroX = Wire.read() << 8 | Wire.read();
    GyroY = Wire.read() << 8 | Wire.read();
    GyroZ = Wire.read() << 8 | Wire.read();
    // Sum all readings
    GyroErrorX = GyroErrorX + (GyroZ / 32.75);
    c++;
  }
  //Divide the sum by 200 to get the error value
  GyroErrorX = GyroErrorX / 200;

  // Print the error values on the Serial Monitor
//  Serial.print("GyroErrorZ: ");
//  Serial.println(GyroErrorX);
}

int count = 0; //temp

// function to decode
void dataDecoder(char c)
{
  LED(4);        //red
  if (c == '\n') // if the endline char
  {
    idflag = true; // start to read the id
    good = false;  // id is not good
    idx = 0;     // reset the index
  }
  else
  {
    if (c == ',') // if comma found
    {
      if (good) // if id is good
      {

        arr[idx] = id.toDouble(); // update the arr
        if (idx == 2)
        {
          newData = true; // set the newdata flag
          tcount = 0;     //when tcount < delay_constant the motor PID will start

//          Serial.println("data recieved");
          startAngle = arr[0]; // do what you want
          endAngle = arr[2];
          travelDis = arr[1];
//          Serial.println("data:" + String(st  artAngle) + " , " + String(endAngle) + " , " + String(travelDis) + ", " + String(angle));
        }
        idx = (idx + 1) % 3; // increment the index
      }
      if (idflag) // if id is getting
      {
        if (id == myID){
          LED(1); //blue
          good = true; // id is good
          delay(20);
          LED(0); //blue
        }
      }
      id = "";        // reset the id
      idflag = false; // id reading done`
    }
    else
      id += c; // append char to the id
  }
  if (Serial.available() > 0)
  {
    dataDecoder(Serial.read());
  }
}

void LED(byte color)
{
  digitalWrite(led_r, color & 1);
  digitalWrite(led_g, (color >> 1) & 1);
  digitalWrite(led_b, (color >> 2) & 1);
}

void intShow()
{

  LED(1); //blue
  pulse(200, 400);
  LED(2); //green
  pulse(200, 400);
  pulse(100, 800);
  LED(4); //red
  pulse(200, 200);
  LED(0);
  delay(1000);
  Serial.begin(9600);  // Setting the baud rate of Serial Monitor (Arduino)
}

void pulse(int pulsetime, int time)
{

  digitalWrite(ML_A1, HIGH);
  digitalWrite(ML_A2, LOW);
  digitalWrite(MR_A1, HIGH);
  digitalWrite(MR_A2, LOW);

  for (int i = 0; i < time; i++)
  {
    digitalWrite(EN_L, HIGH);
    digitalWrite(EN_R, HIGH);
    delayMicroseconds(pulsetime / 10);

    digitalWrite(EN_L, LOW);
    digitalWrite(EN_R, LOW);
    delayMicroseconds(pulsetime * 9 / 10);
  }
}

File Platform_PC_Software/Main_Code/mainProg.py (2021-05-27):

import cv2
import numpy as np
import time
import math
from math import atan
from kalman import kalman
from positioning_algo import positions  
import json
import serial
from multiprocessing import Process, Manager
from serialCom import readSerialData, sendToSerial, serialAutoSend
import movements
from robot import robot
import paho.mqtt.client as mqtt #import the client1
from encrypt import aesEncrypt, aesEncryptString, aesDecrypt
import json
from roboArrangement import  arrageBot
from MQTT_msg_pb2 import *
from flaskServing import *
from helpFunc import *

# swarm id
SWARM_ID = 0;
swarm_name = "platformPC UOP"
BOT_COUNT = 2;
ARENA_DIM = 30;

TOPIC_COM = 'swarm/common'
TOPIC_SEVER_COM = 'swarm/' + str(SWARM_ID) + '/com'
TOPIC_SEVER_BOT_POS = 'swarm/'+ str(SWARM_ID) + '/bot_pos'
connected_clients = []
robots_data = []
newBotPosArr = BotPositionArr()

# image resolutions
img_x = 640
img_y = 480 

# parameters for saving the video
frameRate = 21
dispWidth = 640
dispHeight = 480

# Settings section
serialComEn = True
ipCamEn = True
kalmanEn = False
flaskEn = True
cv2WindowEn = False

# TODO: to be used in future 
# important variables
manager = Manager()
sharedData = manager.list()
sharedData.append("") # json string
sharedData.append("") # json string
sharedData.append(False) # sharedData[2] is the serial broatcasting enable
sharedData.append("")

# com port of the device
comPort = '/dev/ttyUSB0'

# flags
desReachedFlag = False

# making the connection with the seral port
if serialComEn:
    ser = serial.Serial(comPort, 9600, timeout=1, rtscts=1) # connecting to the serial port
    ser.flushInput()   

if ipCamEn:
    cam = cv2.VideoCapture('http://192.168.1.5:8081/video') # video source to capture images
else:
    cam = cv2.VideoCapture(0) # video source to capture images

# robot datas
robotData = {} 
robotDataSet = set()

# position dictonary to bradcast
broadcastPos = {}

#Load the dictionary that was used to generate the markers.
dictionary = cv2.aruco.Dictionary_get(cv2.aruco.DICT_6X6_250)

# Initialize the detector parameters using default values
parameters =  cv2.aruco.DetectorParameters_create()

def battStat():
    batt_lvls = {}
    
    batt_lvls[0] = 85
    batt_lvls[1] = 79 
    
    return json.dumps(batt_lvls)

# on message function
def on_message(client, userdata, message):
    global BOT_COUNT
    # newBotDecode = BotPositionArr.FromString(message.payload)
    decrypted = aesDecrypt(message.payload).decode('utf-8')

    try:
        messageString = decrypted.split(';')
        if message.topic == TOPIC_COM:
            if messageString[1] == 'get_servers':
                print('client requests server name')
                client.publish(TOPIC_COM, aesEncryptString('server_name_response;'+str(SWARM_ID)+';'+swarm_name))
        
        if message.topic == TOPIC_SEVER_COM:
            if messageString[1] == 'connection_req':
                BOT_COUNT = len(robotData)
                print('client requests connection', {'bot_count':BOT_COUNT, 'areana_dim':ARENA_DIM})
                client.publish(TOPIC_SEVER_COM, aesEncryptString('server_response;success;'+ json.dumps({'bot_count':BOT_COUNT, 'areana_dim':ARENA_DIM})), qos = 2)

            if messageString[1] == 'set_dest':
                print("Destination reset")
                destinations = json.loads(messageString[2])
                remapDes(destinations)
                print(destinations)
                arrageBot(robotData , destinations)

            if messageString[1] == 'ping':
                client.publish(TOPIC_SEVER_COM, aesEncryptString('ping;'))
            
            if messageString[1] == 'battStat':
                client.publish(TOPIC_SEVER_COM, aesEncryptString('battStat;' + battStat()))
    except Exception as e :
        # pass
        print("message format error", e)

# saving to a video
#outVid = cv2.VideoWriter('videos/recordings.avi', cv2.VideoWriter_fourcc(*'XVID'),  frameRate, (dispWidth, dispHeight))

# homing sequence
def homeBots():
    homing_seq = sharedData[3]
    if homing_seq:
        # print('home', homing_seq)
        destinations = json.loads(homing_seq)
        arrageBot(robotData , destinations)
        sharedData[3] = ""

# calculate destinations
def destinationCalculation(robots, broadcastPos, frame, client):
    # check homing sequence
    homeBots()
    # create a array to store protobuf information
    newBotPosArr = BotPositionArr()

    # need to optimize
    # print(robots)
    # print(broadcastPos)
    global robot, desReachedFlag
    robots_data = []
    keys = []
    for key, robot_i in robots.items():
        keys.append(key)
        robots_data.append(
            robot(
                    robot_i[0], 0, robot_i[4], 0
            )
        )
    # print(robots_data)
    result = movements.action(robots_data)
    # print('fin',result)

    # count the bots who have reached the destination
    countDesReach = 0

    for i, robot_i in enumerate(result):
        # calculate the direction
        F = robot_i[0]*150000  # resultant force
        # F = min(0.5, F)
        Dir = robot_i[1]  # relustant force direction
        dx = F*math.cos((Dir/180*math.pi))
        dy = F*math.sin((Dir/180*math.pi))
        # print(dx,dy)

        # add the destination circle
        frame = cv2.circle(frame, tuple(robots_data[i].des_pos), 1, (0,255,0), 2)
        # print(frame.shape)
        #print((int(robots_data[i].init_pos[0] + dx), int(robots_data[i].init_pos[1] + dy)))
        frame = cv2.line(frame, (int(robots_data[i].init_pos[0]), int(robots_data[i].init_pos[1])), tuple(robots_data[i].des_pos), (0,255,0), 2)
        frame = cv2.line(frame, (int(robots_data[i].init_pos[0]), int(robots_data[i].init_pos[1])), (int(robots_data[i].init_pos[0]+dx), int(robots_data[i].init_pos[1]+dy)), (0,0,255), 2)

        # calculate the broadcast positions
        broadcastPos[keys[i]] = positions(robots[keys[i]][0], robots[keys[i]][3], [robots_data[i].init_pos[0] + dx, robots_data[i].init_pos[1] + dy], 0)

        # prepare data to send through mqtt
        newBot = BotPosition()
        newBot.bot_id = i
        newBot.x_cod = robots_data[i].init_pos[0]/img_x*30 
        newBot.y_cod = robots_data[i].init_pos[1]/img_y*30
        newBot.angle = 0
        newBotPosArr.positions.append(newBot)

        # print(distanceTwoPoints((int(robots_data[i].init_pos[0]), int(robots_data[i].init_pos[1])), tuple(robots_data[i].des_pos)))
        if 40<distanceTwoPoints((int(robots_data[i].init_pos[0]), int(robots_data[i].init_pos[1])), tuple(robots_data[i].des_pos)):
            countDesReach += 1
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

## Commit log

2020-07-27 done some error corrections
    [mainProg.py]
2020-08-13 gyro , motor, tuning PID
2020-08-13 gyro, motor citntrol, PID with comments
2020-08-14 turning and moving routines are done, direction correcting,
    [main.cpp]
2020-08-21 3d model partialy finished
    [18650.SLDPRT, 18650BatteryCase v6.step, Assembly.SLDASM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]
2020-08-22 finalize the solid model
    [Base.SLDPRT, FullAssembly.SLDASM, Motor_Bracket_Assembly.SLDASM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]
2020-08-22 done some error corrections in bot code
    [main.cpp]
2020-11-08 stl loader added
    [Cover.91c86dd7.STL, Cover.STL, motor.STL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]
2020-11-08 added vertual environment and added the new swarm dashboard
    [Cover.ce95700d.STL]
2020-11-08 done some changes in venv
    [pyvenv.cfg]
2020-11-09 orbit controls and mouse event colisions handled
    [Cover.91c86dd7.STL]
2020-11-10 cleaning unnesassary files
    [pyvenv.cfg]
2020-11-11 done some changes to the web app
    [Cover.91c86dd7.STL]
2021-01-29 upated 3dInterface
    [Cover.91c86dd7.STL]
2021-01-31 battery status implemented
2021-01-31 battery status updated
2021-02-02 fiexed some minor ui issues
    [encrypt.py, field.py, main.cpp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]
2021-02-02 done some debugging in website
    [Cover.ce95700d.STL]
2021-02-02 Algorithm Unit Testing Added.
    [Cover.ce95700d.STL]
2021-03-09 change the 3js interface
    [Cover.91c86dd7.STL]
2021-05-22 added functionality to the buttons
2021-05-23 status led image updated
2021-05-28 Gerber files and PCB scemetics are added
2021-05-28 laser cutting files added
    [bot.dxf]
